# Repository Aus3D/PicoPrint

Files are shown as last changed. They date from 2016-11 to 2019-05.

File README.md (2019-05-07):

# PicoPrint

PicoPrint is a 32-bit 3D printer control board, designed to be fast, quiet, and compact.

PicoPrint is still in active development, and some specifications are not yet finalised. Once the design has been finalised, this page will be updated with detailed information.

## Image
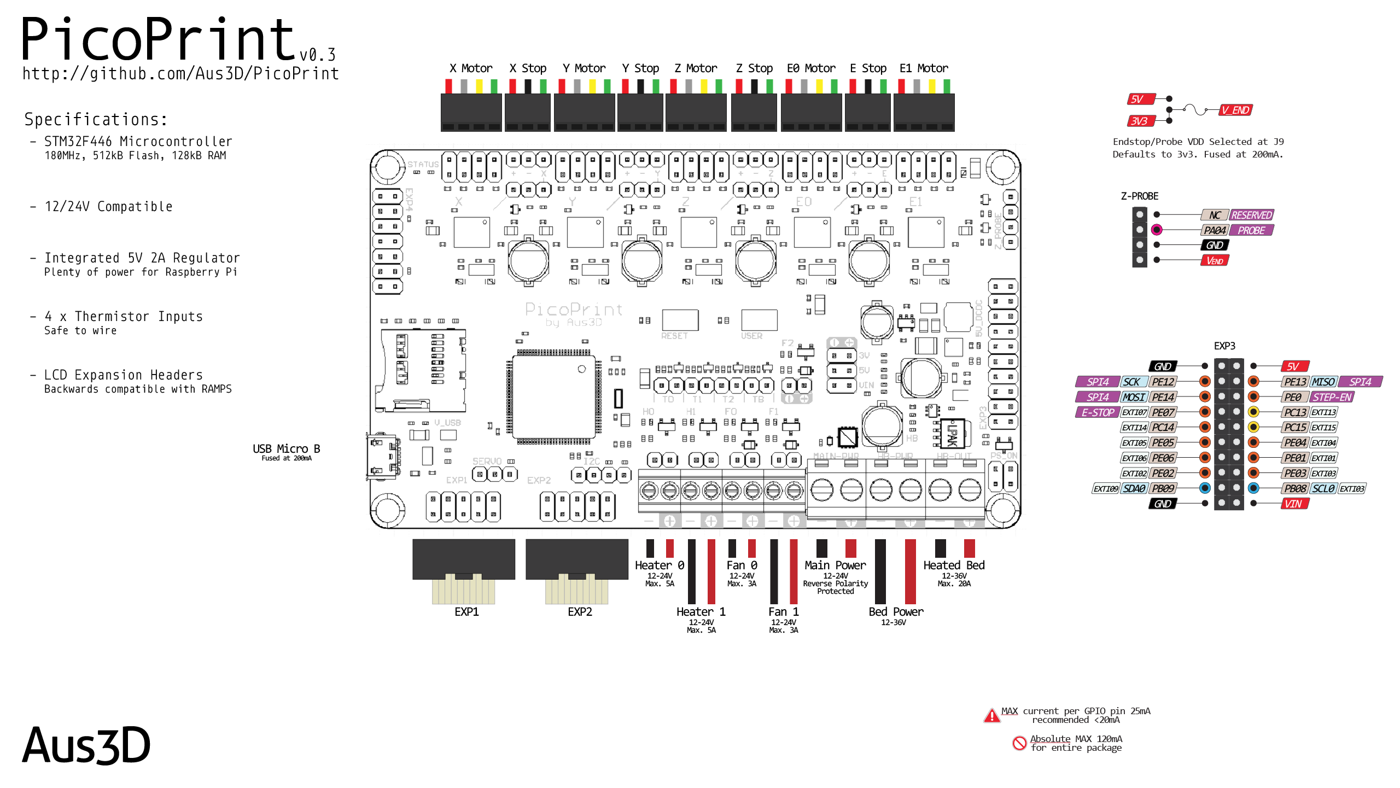
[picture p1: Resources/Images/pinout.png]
PicoPrint Pinout


## Specifications
* 32-bit STM32F446VET6 Microcontroller
  * 180MHz core clock speed
  * 512kB Flash Memory
  * 128kB SRAM
  * Floating Point Unit
* 5 x TMC2130 Stepper Drivers
  * STEP/DIR for motion + SPI bus for configuration
  * StealthChop for quiet printing
  * StallGuard signal wired to endstop inputs for sensorless homing (enabled by jumper)
* 1 x 20A MOSFET for Heated Bed
  * Low RDSon MOSFET for minimum heat dissipation
  * MOSFET driver IC for improved PWM performance
* 2 x 5A MOSFETs for Heater Cartridges
  * Accessible via screw terminal or pin header for pluggable cables
* 3 x 3A MOSFETs for Fans and Lighting
  * Suppresion diodes for flyback protection
  * Accessible via screw terminal (F0 & F1) or pin header (F0, F1 & F2)
* 12-24V Compatibility
  * Maximum 30V on main power rail
  * Maximum 40V on bed power rail
* Internal 5V 2A High-Efficiency Buck Regulator
  * Synchronous regulator for maximum efficiency
  * Up to 2A current draw
    * 200mA required for PicoPrint, 1.8A remaining for peripherals
    * Sufficient for most external LCDs, RC servo motors, or single-board computers (Raspberry Pi and similar)
* 4 x Thermistor Inputs
  * 2 HotEnds, 1 Bed + 1 Chamber/Spare
* 4 x Endstop Inputs
  * Jumper allows selection of either external endstop or TMC2130 StallGuard for sensorless homing for each endstop
* 1 x Z-Probe Connector
  * Includes 1 Interrupt-capable pin and one ADC-capable pin
* Rugged Design for Maximum Reliability
  * Power Rail Protection
    * Main power input is protected against reverse-polarity by P-Ch MOSFET
      * No fuse to replace if wiring is reversed
      * Red LED indicates reversed power polarity
    * 5V from USB is fused (200mA self-resetting PTC) to protect host device
    * 5V Buck Regulator implements overcurrent, overtemperature, and short-circuit protection
    * 3.3V Linear Regulator implements overcurrent and overtemperature protection
    * Main power input can be monitored by ADC channel to measure input voltage (firmware dependent)
  * Microcontroller Pin Protection
    * Dedicated ESD-protection IC on USB interface
    * Thermistors + Endstops + Z-Probe protected against accidental connection to ±30V by diode clipping circuit
      * Endstops are safe to use with 5/12/24V signals if desired

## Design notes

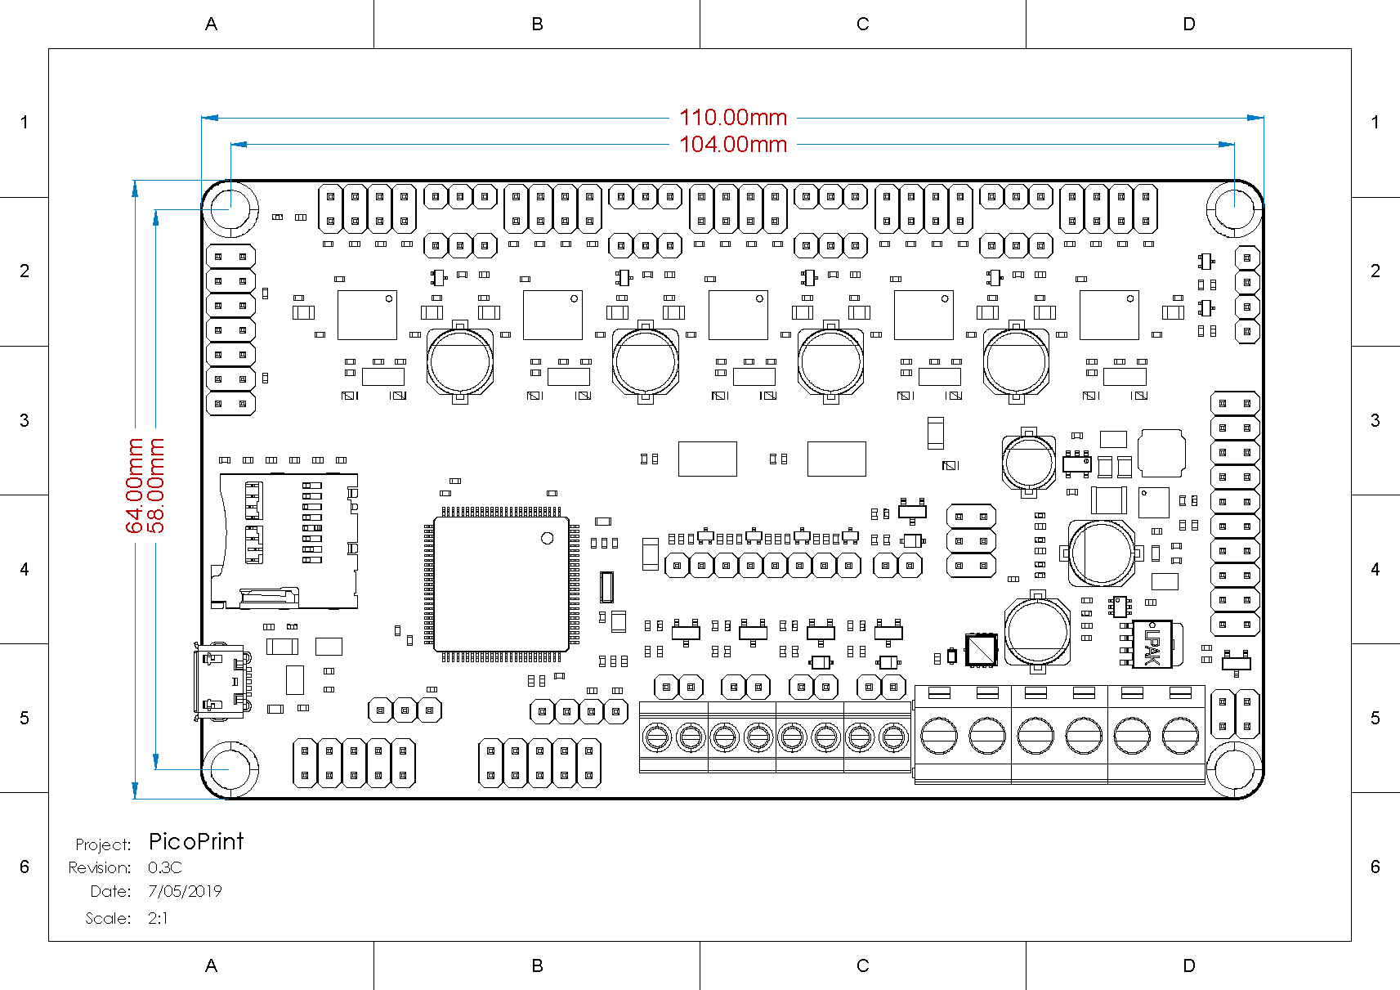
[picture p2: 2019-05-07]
Resources/Images/dimensions.png

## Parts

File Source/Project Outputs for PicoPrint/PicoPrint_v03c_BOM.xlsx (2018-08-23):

Designator | Description | Comment | Value | Quantity | Note | Manufacturer 1 | Manufacturer Part Number 1 | Supplier 1 | Supplier Part Number 1
C1, C8, C13, C14, C18, C25, C27, C48, C52, C56, C88, C92, C122, C123 | Capacitor (SMD Ceramic) | CapC-0402-4.7uF-10V | 4.7uF | 14 | Approved sub OK | Samsung (https://octopart-clicks.com/click/altium?sku=1276-1482-1-ND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) | CL05A475MP5NRNC (https://octopart-clicks.com/click/altium?sku=1276-1482-1-ND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) | Digi-Key | 1276-1482-1-ND (https://octopart-clicks.com/click/altium?sku=1276-1482-1-ND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)
C2, C3, C4, C5, C6, C7, C9, C11, C12, C19, C20, C21, C22, C23, C24, C45, C49, C53, C63, C64, C65, C72, C73, C74, C85, C89, C101, C102, C107, C108, C115, C124 | Capacitor (SMD Ceramic) | CapC-0402-100nF | 100nF | 32 | Approved sub OK | Yageo (https://octopart-clicks.com/click/altium?sku=311-1336-1-ND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) | CC0402KRX5R6BB104 (https://octopart-clicks.com/click/altium?sku=311-1336-1-ND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) | Digi-Key | 311-1336-1-ND (https://octopart-clicks.com/click/altium?sku=311-1336-1-ND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)
C10, C15, C16, C26 | Capacitor (SMD Ceramic) | CapC-0402-1uF-10V | 1uF | 4 | Approved sub OK | Samsung (https://octopart-clicks.com/click/altium?sku=1276-1448-1-ND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) | CL05A105MP5NNNC (https://octopart-clicks.com/click/altium?sku=1276-1448-1-ND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) | Digi-Key | 1276-1448-1-ND (https://octopart-clicks.com/click/altium?sku=1276-1448-1-ND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)
C17 | Capacitor (SMD Ceramic) | CapC-0805-10uF 6.3V | 10uF | 1 | Approved sub OK | Samsung (https://octopart-clicks.com/click/altium?sku=1276-6457-1-ND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) | CL21A106KQFNNNG (https://octopart-clicks.com/click/altium?sku=1276-6457-1-ND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) | Digi-Key | 1276-6457-1-ND (https://octopart-clicks.com/click/altium?sku=1276-6457-1-ND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)
C29, C31, C33, C75, C77 | Capacitor (SMD Ceramic) | CapC-0402-22nF-50V | 22nF | 5 | Approved sub OK | Murata (https://octopart-clicks.com/click/altium?sku=490-3884-1-ND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) | GRM155R71H223KA12D (https://octopart-clicks.com/click/altium?sku=490-3884-1-ND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) | Digi-Key | 490-3884-1-ND (https://octopart-clicks.com/click/altium?sku=490-3884-1-ND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)
C30, C32, C34, C35, C36, C39, C40, C42, C43, C76, C78, C79, C80, C82, C83, C113, C117 | Capacitor (SMD Ceramic) | CapC-0402-100nF-50V | 100nF | 17 | Approved sub OK | Murata (https://octopart-clicks.com/click/altium?sku=490-10700-1-ND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) | GRM155R71H104KE14D (https://octopart-clicks.com/click/altium?sku=490-10700-1-ND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) | Digi-Key | 490-10700-1-ND (https://octopart-clicks.com/click/altium?sku=490-10700-1-ND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)
C37, C38, C41, C44, C81, C84, C110, C114, C125, C126, C127 | Capacitor (SMD Ceramic) | CapC-0603-1uF 50V | 1uF | 11 | Approved sub OK | Samsung (https://octopart-clicks.com/click/altium?sku=1276-1860-1-ND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) | CL10A105KB8NNNC (https://octopart-clicks.com/click/altium?sku=1276-1860-1-ND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) | Digi-Key | 1276-1860-1-ND (https://octopart-clicks.com/click/altium?sku=1276-1860-1-ND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)
C46, C50, C54, C86, C90 | Capacitor (SMD Ceramic) | CapC-0402-470nF | 470nF | 5 | Approved sub OK | Samsung (https://octopart-clicks.com/click/altium?sku=1276-1173-1-ND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) | CL05A474KP5NNNC (https://octopart-clicks.com/click/altium?sku=1276-1173-1-ND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) | Digi-Key | 1276-1173-1-ND (https://octopart-clicks.com/click/altium?sku=1276-1173-1-ND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)
C57, C58, C59, C60, C61, C62, C66, C67, C68, C69, C70, C71, C97, C98, C99, C100, C103, C104, C105, C106 | Capacitor (SMD Ceramic) | CapC-0402-470pF-100V | 470pF | 20 | Approved sub OK | Murata (https://octopart-clicks.com/click/altium?sku=490-6369-1-ND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) | GRM155R72A471KA01D (https://octopart-clicks.com/click/altium?sku=490-6369-1-ND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) | Digi-Key | 490-6369-1-ND (https://octopart-clicks.com/click/altium?sku=490-6369-1-ND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)
C93, C94, C95, C96, C112, C118 | Capacitor (SMD Polarised Electrolytic) | CapE-6.3-100uF-35V | 100uF 35V | 6 | Approved sub OK | Panasonic (https://octopart-clicks.com/click/altium?sku=PCE5016CT-ND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) | EEE-FT1V101AP (https://octopart-clicks.com/click/altium?sku=PCE5016CT-ND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) | Digi-Key | PCE5016CT-ND (https://octopart-clicks.com/click/altium?sku=PCE5016CT-ND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)
C116 | Capacitor (SMD Polarised Electrolytic) | CapE-5.0-100uF-6.3V | 100uF 6.3V | 1 | Approved sub OK | United Chemi-Con (https://octopart-clicks.com/click/altium?manufacturer=United%20Chemi-Con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) | EMVA6R3ADA101ME55G (https://octopart-clicks.com/click/altium?manufacturer=United%20Chemi-Con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) | Digi-Key | 565-2057-1-ND (https://octopart-clicks.com/click/altium?manufacturer=United%20Chemi-Con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)
C119 | Capacitor (SMD Ceramic) | CapC-1210-4.7uF-50V | 4.7uF | 1 | Approved sub OK | Murata (https://octopart-clicks.com/click/altium?sku=490-1864-1-ND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) | GRM32ER71H475KA88L (https://octopart-clicks.com/click/altium?sku=490-1864-1-ND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) | Digi-Key | 490-1864-1-ND (https://octopart-clicks.com/click/altium?sku=490-1864-1-ND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)
C120, C121 | Capacitor (SMD Ceramic) | CapC-0805-22uF 6.3V | 22uF | 2 | Approved sub OK | Samsung (https://octopart-clicks.com/click/altium?sku=1276-6460-1-ND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) | CL21A226MQQNNNG (https://octopart-clicks.com/click/altium?sku=1276-6460-1-ND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) | Digi-Key | 1276-6460-1-ND (https://octopart-clicks.com/click/altium?sku=1276-6460-1-ND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)
D1, D2, D3, D4, D5, D6, D7, D8, D9, D10 | Diode (SMD) | Dual Schottky 100mA 30V SOT523 |  | 10 | Approved sub OK | MCC (https://octopart-clicks.com/click/altium?sku=BAT54ST-TPCT-ND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) | BAT54ST-TP (https://octopart-clicks.com/click/altium?sku=BAT54ST-TPCT-ND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) | Digi-Key | BAT54ST-TPCT-ND (https://octopart-clicks.com/click/altium?sku=BAT54ST-TPCT-ND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)
D11, D12, D13 | Diode (SMD) | General 500mW 75V SOD323 | Vf=1V @ 50mA | 3 | Approved sub OK | MCC (https://octopart-clicks.com/click/altium?sku=1N4148WXTPMSCT-ND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) | 1N4148WX-TP (https://octopart-clicks.com/click/altium?sku=1N4148WXTPMSCT-ND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) | Digi-Key | 1N4148WXTPMSCT-ND (https://octopart-clicks.com/click/altium?sku=1N4148WXTPMSCT-ND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)
D14, D15, D16 | Diode (SMD) | Schottky 2A 40V SOD-123F |  | 3 | Approved sub OK | ON Semiconductor / Fairchild (https://octopart-clicks.com/click/altium?manufacturer=ON%20Semiconductor%20%2F%20Fairchild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) | SS24FL (https://octopart-clicks.com/click/altium?manufacturer=ON%20Semiconductor%20%2F%20Fairchild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) | Digi-Key | SS24FLCT-ND (https://octopart-clicks.com/click/altium?manufacturer=ON%20Semiconductor%20%2F%20Fairchild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)
D17 | Diode (SMD) | Zener 10V 150mW SOD523 |  | 1 | Approved sub OK | Panasonic SSG (https://octopart-clicks.com/click/altium?sku=DZ2S100M0LCT-ND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) | DZ2S100M0L (https://octopart-clicks.com/click/altium?sku=DZ2S100M0LCT-ND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) | Digi-Key | DZ2S100M0LCT-ND (https://octopart-clicks.com/click/altium?sku=DZ2S100M0LCT-ND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)
F1, F3 | Fuse - 30V 400mA Trip PTC SMD 1206 | PTC Resettable Fuse | 200mA | 2 | Approved sub OK | Bel (https://octopart-clicks.com/click/altium?sku=507-1797-1-ND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) | 0ZCJ0020FF2E (https://octopart-clicks.com/click/altium?sku=507-1797-1-ND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) | Digi-Key | 507-1797-1-ND (https://octopart-clicks.com/click/altium?sku=507-1797-1-ND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)
FB1, FB3, FB4 | Ferrite bead 120 Ohm at 100 MHz 2A 0603 SMD | 120R @ 100 MHz | 120R @ 100 MHz | 3 | Approved sub OK, [NoParam] | Murata (https://octopart-clicks.com/click/altium?sku=490-1037-1-ND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) | BLM18PG-121SN1D (https://octopart-clicks.com/click/altium?sku=490-1037-1-ND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) | Digi-Key | 490-1037-1-ND (https://octopart-clicks.com/click/altium?sku=490-1037-1-ND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)
FB2 | Ferrite bead 50 Ohm at 100 MHz 6A 1206 SMD | 50R @ 100 MHz | 50R @ 100 MHz | 1 | Approved sub OK | Laird (https://octopart-clicks.com/click/altium?sku=240-2412-1-ND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) | HI1206T500R-10 (https://octopart-clicks.com/click/altium?sku=240-2412-1-ND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) | Digi-Key | 240-2412-1-ND (https://octopart-clicks.com/click/altium?sku=240-2412-1-ND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)
J1 |  | Micro-USB B Socket |  | 1 | Approved sub OK | Molex (https://octopart-clicks.com/click/altium?sku=WM1399CT-ND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) | 105017-0001 (https://octopart-clicks.com/click/altium?sku=WM1399CT-ND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) | Digi-Key | WM1399CT-ND (https://octopart-clicks.com/click/altium?sku=WM1399CT-ND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)
L2 | 4.7µH Shielded Wirewound Inductor 2.6A 35 mOhm Nonstandard | Inductor SMD 4.7uH 2.6A | 4.7uH | 1 | Approved sub OK | Taiyo Yuden (https://octopart-clicks.com/click/altium?sku=587-3461-1-ND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) | NRS5030T4R7MMGJ (https://octopart-clicks.com/click/altium?sku=587-3461-1-ND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) | Digi-Key | 587-3461-1-ND (https://octopart-clicks.com/click/altium?sku=587-3461-1-ND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)
LD1 | LED (SMD) | LED-0402 | Red | 1 | Approved sub OK | Wurth Electronics (https://octopart-clicks.com/click/altium?sku=732-11991-1-ND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) | 150040RS73240 (https://octopart-clicks.com/click/altium?sku=732-11991-1-ND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) | Digi-Key | 732-11991-1-ND (https://octopart-clicks.com/click/altium?sku=732-11991-1-ND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)
LD2, LD3, LD4, LD5, LD6, LD8, LD9, LD10, LD11, LD12, LD13 | LED (SMD) | LED-0402 | Green | 11 | Approved sub OK | Wurth Electronics (https://octopart-clicks.com/click/altium?sku=732-11992-1-ND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) | 150040VS73240 (https://octopart-clicks.com/click/altium?sku=732-11992-1-ND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) | Digi-Key | 732-11992-1-ND (https://octopart-clicks.com/click/altium?sku=732-11992-1-ND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)
LD7 | LED (SMD) | LED-0402 | Yellow | 1 | Approved sub OK | Wurth Electronics (https://octopart-clicks.com/click/altium?sku=732-11993-1-ND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) | 150040YS73240 (https://octopart-clicks.com/click/altium?sku=732-11993-1-ND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) | Digi-Key | 732-11993-1-ND (https://octopart-clicks.com/click/altium?sku=732-11993-1-ND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)
P1, P4, P11 | Screw Terminal 5mm 2-Way | Main PWR Screw Term, Bed PWR Screw Term, HB Screw Term |  | 3 |  | Phoenix Contact (https://octopart-clicks.com/click/altium?sku=277-6405-ND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) | 1935776 (https://octopart-clicks.com/click/altium?sku=277-6405-ND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) | Digi-Key | 277-6405-ND (https://octopart-clicks.com/click/altium?sku=277-6405-ND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)
P2, P3, P6, P9, P29, P37, P38, P39, P40 | Header, 3-Pin | X-STOP, E-STOP, Y_STOP, Z-STOP, SERVO, X_STOP_SEL, Y_STOP_SEL, Z_STOP_SEL, E_STOP_SEL |  | 9 | Approved sub OK | Generic Header
P5, P10 | Header, 5-Pin, Dual row | EXP1, EXP2 |  | 2 | Approved sub OK | Generic Header
P7, P28 | Header, 3-Pin, Dual row | PWR_AUX, Header 2X2 |  | 2 | Approved sub OK | Generic Header
P8, P30 | Header, 4-Pin | PROBE, I2C |  | 2 | Approved sub OK | Generic Header
P12, P16, P19, P24, P32 | Header, 2-Pin | H0 Header, H1 Header, F0 Header, F1 Header, F2 Header |  | 5 | Approved sub OK | Generic Header
P13 | Header, 10-Pin, Dual row | EXP3 |  | 1 | Approved sub OK | Generic Header
P14 | Header, 8-Pin | Thermistors |  | 1 | Approved sub OK | Generic Header
P15, P17, P22, P26 | Screw Terminal 3.5mm 2-Way | H0 Screw Term, H1 Screw Term, F0 Screw Term, F1 Screw Term |  | 4 |  | Phoenix Contact (https://octopart-clicks.com/click/altium?sku=277-1721-ND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) | 1984617 (https://octopart-clicks.com/click/altium?sku=277-1721-ND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) | Digi-Key | 277-1721-ND (https://octopart-clicks.com/click/altium?sku=277-1721-ND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)
P18 | Header, 7-Pin, Dual row | EXP4 |  | 1 | Approved sub OK | Generic Header
P20, P23, P27, P33, P35 | Header, 4-Pin, Dual row | X-MOTOR, Y-MOTOR, Z-MOTOR, E0-MOTOR, E1-MOTOR |  | 5 | Approved sub OK | Generic Header
Q1, Q2, Q3, Q4, Q8, Q9 | N-CH MOSFET 30V 5.7A SOT23 | AO3400A |  | 6 |  | Alpha & Omega Semiconductor (https://octopart-clicks.com/click/altium?manufacturer=Alpha%20%26%20Omega%20Semiconductor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) | AO3400A (https://octopart-clicks.com/click/altium?manufacturer=Alpha%20%26%20Omega%20Semiconductor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) | Digi-Key | 785-1000-1-ND (https://octopart-clicks.com/click/altium?manufacturer=Alpha%20%26%20Omega%20Semiconductor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)
Q5 | N-CH MOSFET 40V 100A LFPAK | BUK9Y4R4-40E |  | 1 |  | NXP Semiconductors (https://octopart-clicks.com/click/altium?manufacturer=NXP%20Semiconductors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) | BUK9Y4R4-40E,115 (https://octopart-clicks.com/click/altium?manufacturer=NXP%20Semiconductors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) | Digi-Key | 1727-1502-1-ND (https://octopart-clicks.com/click/altium?manufacturer=NXP%20Semiconductors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)
Q7 | MOSFET SMD P-CH 30V 60A PowerPAK1212 | SI7111EDN-T1-GE3 |  | 1 |  | Vishay (https://octopart-clicks.com/click/altium?sku=SI7111EDN-T1-GE3CT-ND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) | SI7111EDN-T1-GE3 (https://octopart-clicks.com/click/altium?sku=SI7111EDN-T1-GE3CT-ND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) | Digi-Key | SI7111EDN-T1-GE3CT-ND (https://octopart-clicks.com/click/altium?sku=SI7111EDN-T1-GE3CT-ND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)
R1, R2, R8, R13, R15, R20, R22, R25, R28, R32, R34 | Resistor | Res-0402-4K7 | 4K7 | 11 | Approved sub OK | Yageo (https://octopart-clicks.com/click/altium?sku=311-4.7KJRCT-ND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) | RC0402JR-074K7L (https://octopart-clicks.com/click/altium?sku=311-4.7KJRCT-ND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) | Digi-Key | 311-4.7KJRCT-ND (https://octopart-clicks.com/click/altium?sku=311-4.7KJRCT-ND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)
R3, R4, R5, R19, R37, R38, R43, R44, R48, R51, R53, R68 | Resistor | Res-0402-1K | 1K | 12 | Approved sub OK | Yageo (https://octopart-clicks.com/click/altium?sku=311-1.0KJRCT-ND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) | RC0402JR-071KL (https://octopart-clicks.com/click/altium?sku=311-1.0KJRCT-ND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) | Digi-Key | 311-1.0KJRCT-ND (https://octopart-clicks.com/click/altium?sku=311-1.0KJRCT-ND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)
R6, R7, R14 | Resistor | Res-0402-470R | 470R | 3 | Approved sub OK | Yageo (https://octopart-clicks.com/click/altium?sku=311-470JRCT-ND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) | RC0402JR-07470RL (https://octopart-clicks.com/click/altium?sku=311-470JRCT-ND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) | Digi-Key | 311-470JRCT-ND (https://octopart-clicks.com/click/altium?sku=311-470JRCT-ND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)
R9, R10 | Resistor | Res-0402-2K2 | 2K2 | 2 | Approved sub OK | Yageo (https://octopart-clicks.com/click/altium?sku=311-2.2KJRCT-ND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) | RC0402JR-072K2L (https://octopart-clicks.com/click/altium?sku=311-2.2KJRCT-ND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) | Digi-Key | 311-2.2KJRCT-ND (https://octopart-clicks.com/click/altium?sku=311-2.2KJRCT-ND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)
R11, R12 | Resistor | Res-0402-100R | 100R | 2 | Approved sub OK | Yageo (https://octopart-clicks.com/click/altium?sku=311-100JRCT-ND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) | RC0402JR-07100RL (https://octopart-clicks.com/click/altium?sku=311-100JRCT-ND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) | Digi-Key | 311-100JRCT-ND (https://octopart-clicks.com/click/altium?sku=311-100JRCT-ND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)
R16, R17, R70 | Resistor | Res-0402-47K | 47K | 3 | Approved sub OK | Yageo (https://octopart-clicks.com/click/altium?sku=311-47KJRCT-ND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) | RC0402JR-0747KL (https://octopart-clicks.com/click/altium?sku=311-47KJRCT-ND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) | Digi-Key | 311-47KJRCT-ND (https://octopart-clicks.com/click/altium?sku=311-47KJRCT-ND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)
R18, R21, R23, R26, R65, R69 | Resistor | Res-0402-10K | 10K | 6 | Approved sub OK | Yageo (https://octopart-clicks.com/click/altium?sku=311-10KJRCT-ND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) | RC0402JR-0710KL (https://octopart-clicks.com/click/altium?sku=311-10KJRCT-ND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) | Digi-Key | 311-10KJRCT-ND (https://octopart-clicks.com/click/altium?sku=311-10KJRCT-ND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)
R24, R27, R31, R33 | Resistor | Res-0402-4K7 | 4K7 1% | 4 | Approved sub OK | Yageo (https://octopart-clicks.com/click/altium?sku=311-4.7KJRCT-ND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) | RC0402JR-074K7L (https://octopart-clicks.com/click/altium?sku=311-4.7KJRCT-ND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) | Digi-Key | 311-4.7KJRCT-ND (https://octopart-clicks.com/click/altium?sku=311-4.7KJRCT-ND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)
R29, R30 | Resistor | Res-0402-22R | 22R | 2 | Approved sub OK | Yageo (https://octopart-clicks.com/click/altium?sku=311-22JRCT-ND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) | RC0402JR-0722RL (https://octopart-clicks.com/click/altium?sku=311-22JRCT-ND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) | Digi-Key | 311-22JRCT-ND (https://octopart-clicks.com/click/altium?sku=311-22JRCT-ND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)
R35, R36, R41, R42, R47, R50 | Resistor | Res-0402-10R | 10R | 6 | Approved sub OK | Yageo (https://octopart-clicks.com/click/altium?sku=311-10JRCT-ND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) | RC0402JR-0710RL (https://octopart-clicks.com/click/altium?sku=311-10JRCT-ND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) | Digi-Key | 311-10JRCT-ND (https://octopart-clicks.com/click/altium?sku=311-10JRCT-ND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)
R39, R40, R45, R46, R49, R52, R54, R67 | Resistor | Res-0402-100K | 100K | 8 | Approved sub OK | Yageo (https://octopart-clicks.com/click/altium?sku=311-100KJRCT-ND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) | RC0402JR-07100KL (https://octopart-clicks.com/click/altium?sku=311-100KJRCT-ND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) | Digi-Key | 311-100KJRCT-ND (https://octopart-clicks.com/click/altium?sku=311-100KJRCT-ND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)
R55, R56, R57, R58, R59, R60, R61, R62, R63, R64 | Resistor | Res-0805-0R11-0.333W | 0R11 1% | 10 | Approved sub OK | Susumu (https://octopart-clicks.com/click/altium?sku=RL12S.11FCT-ND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) | RL1220S-R11-F (https://octopart-clicks.com/click/altium?sku=RL12S.11FCT-ND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) | Digi-Key | RL12S.11FCT-ND (https://octopart-clicks.com/click/altium?sku=RL12S.11FCT-ND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)
R66 | Resistor | Res-0402-49.9K | 49.9K | 1 | Approved sub OK | Yageo (https://octopart-clicks.com/click/altium?sku=311-2296-1-ND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) | RT0402DRE0749K9L (https://octopart-clicks.com/click/altium?sku=311-2296-1-ND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) | Digi-Key | 311-2296-1-ND (https://octopart-clicks.com/click/altium?sku=311-2296-1-ND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)
S1, S2 | SMD Button | User, Reset |  | 2 | Approved sub OK | APEM (https://octopart-clicks.com/click/altium?sku=679-2396-1-ND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) | MJTP1106SATR (https://octopart-clicks.com/click/altium?sku=679-2396-1-ND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) | Digi-Key | 679-2396-1-ND (https://octopart-clicks.com/click/altium?sku=679-2396-1-ND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)
U1 | ARM Cortex-M4 32-bit MCU+FPU, 210 DMIPS, 512 kB Flash, 128 kB Internal RAM, 81 I/Os, 100-pin LQFP, -40 to 105 degC, Tray | STM32F446VET6 |  | 1 |  | STMicroelectronics (https://octopart-clicks.com/click/altium?sku=497-15375-ND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) | STM32F446VET6 (https://octopart-clicks.com/click/altium?sku=497-15375-ND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) | Digi-Key | 497-15375-ND (https://octopart-clicks.com/click/altium?sku=497-15375-ND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)
U2 | MicroSD Card Socket | MICROSD |  | 1 | Approved sub OK | Amphenol (https://octopart-clicks.com/click/altium?sku=101-00660-68-6-1-ND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) | 10100660686 (https://octopart-clicks.com/click/altium?sku=101-00660-68-6-1-ND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) | Digi-Key | 101-00660-68-6-1-ND (https://octopart-clicks.com/click/altium?sku=101-00660-68-6-1-ND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)
U3 | ESD Protection IC | USBLC6 USB ESD Protection |  | 1 |  | STMicroelectronics (https://octopart-clicks.com/click/altium?sku=497-5235-1-ND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) | USBLC6-2SC6 (https://octopart-clicks.com/click/altium?sku=497-5235-1-ND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) | Digi-Key | 497-5235-1-ND (https://octopart-clicks.com/click/altium?sku=497-5235-1-ND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)
U4 | MOSFET Gate Driver IC | Gate Driver |  | 1 |  | Diodes (https://octopart-clicks.com/click/altium?sku=ZXGD3009DYTADICT-ND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) | ZXGD3009DYTA (https://octopart-clicks.com/click/altium?sku=ZXGD3009DYTADICT-ND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) | Digi-Key | ZXGD3009DYTADICT-ND (https://octopart-clicks.com/click/altium?sku=ZXGD3009DYTADICT-ND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)
U5, U6, U7, U8, U9 | Stepper Driver IC | TMC2130-LA |  | 5 |  | Trinamic (https://octopart-clicks.com/click/altium?sku=1460-1130-1-ND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) | TMC2130-LA-T (https://octopart-clicks.com/click/altium?sku=1460-1130-1-ND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) | Digi-Key | 1460-1130-1-ND (https://octopart-clicks.com/click/altium?sku=1460-1130-1-ND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)
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

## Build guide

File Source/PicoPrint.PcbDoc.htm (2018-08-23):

Reporting Options

# File in Previous Format

Date | : | 23/08/2018
Time | : | 1:22:07 PM
Filename | : | G:\Git\R32-Micro\Source\PicoPrint.PcbDoc

Version | Warning

This file was generated by an earlier version of the software

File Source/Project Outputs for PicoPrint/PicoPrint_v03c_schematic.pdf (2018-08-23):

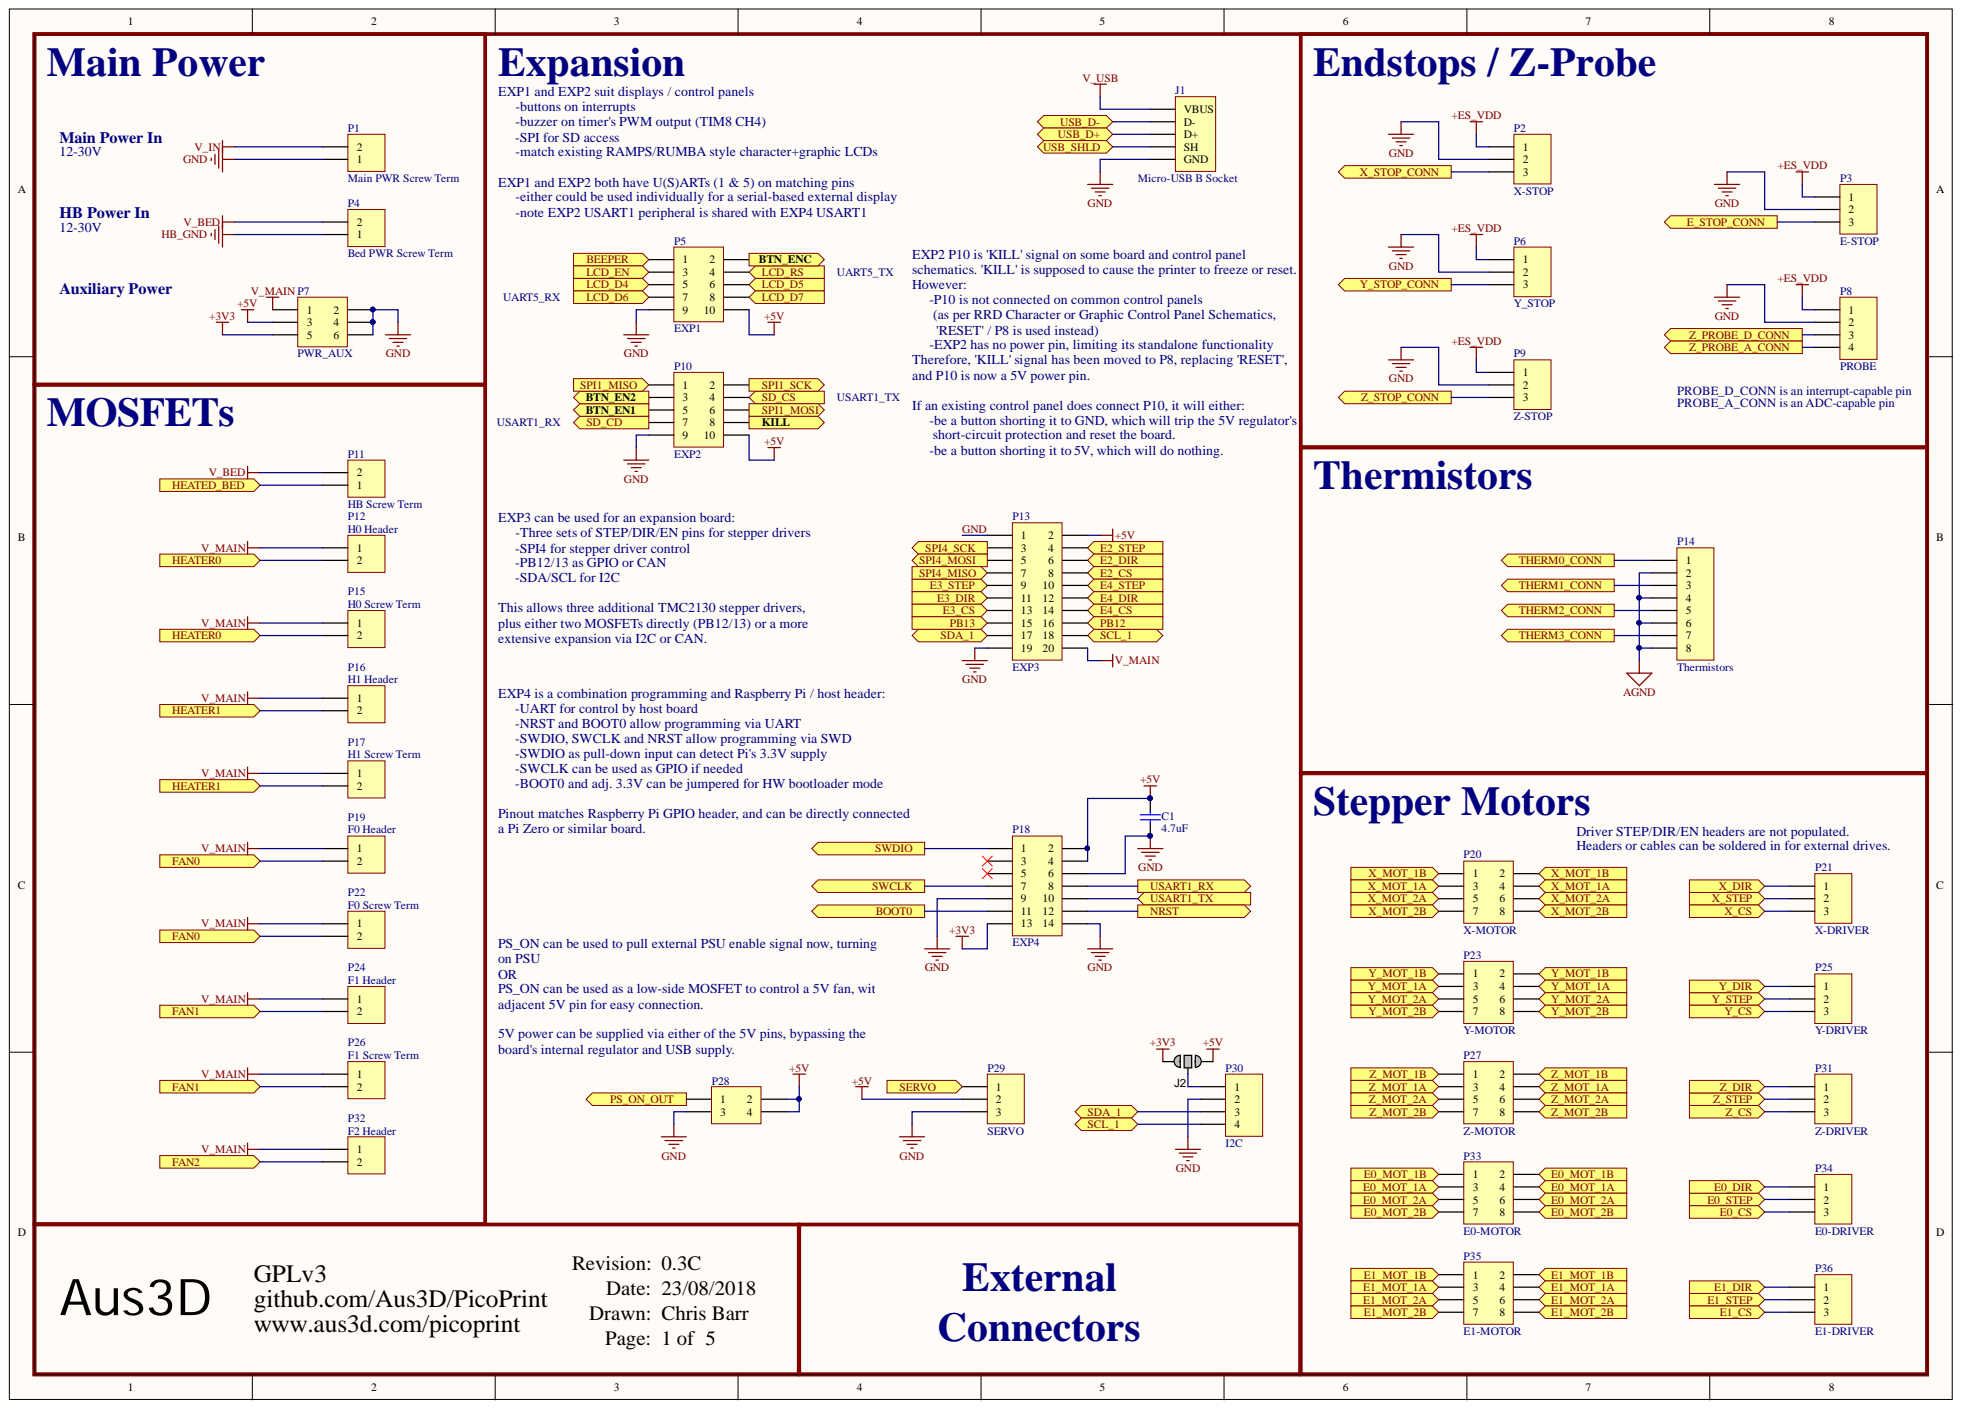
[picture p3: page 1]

EXP1 and EXP2 suit displays / control panels
-buttons on interrupts
-buzzer on timer's PWM output (TIM8 CH4)
-SPI for SD access
-match existing RAMPS/RUMBA style character+graphic LCDs

EXP1 and EXP2 both have U(S)ARTs (1 & 5) on matching pins
-either could be used individually for a serial-based external display
-note EXP2 USART1 peripheral is shared with EXP4 USART1

EXP2 P10 is 'KILL' signal on some board and control panel
schematics. 'KILL' is supposed to cause the printer to freeze or reset.
However:
-P10 is not connected on common control panels
(as per RRD Character or Graphic Control Panel Schematics,
'RESET' / P8 is used instead)
-EXP2 has no power pin, limiting its standalone functionality
Therefore, 'KILL' signal has been moved to P8, replacing 'RESET',
and P10 is now a 5V power pin.

PROBE_D_CONN is an interrupt-capable pin
PROBE_A_CONN is an ADC-capable pin

If an existing control panel does connect P10, it will either:
-be a button shorting it to GND, which will trip the 5V regulator's
short-circuit protection and reset the board.
-be a button shorting it to 5V, which will do nothing.

EXP3 can be used for an expansion board:
-Three sets of STEP/DIR/EN pins for stepper drivers
-SPI4 for stepper driver control
-PB12/13 as GPIO or CAN
-SDA/SCL for I2C

This allows three additional TMC2130 stepper drivers,
plus either two MOSFETs directly (PB12/13) or a more
extensive expansion via I2C or CAN.

EXP4 is a combination programming and Raspberry Pi / host header:
-UART for control by host board
-NRST and BOOT0 allow programming via UART
-SWDIO, SWCLK and NRST allow programming via SWD
-SWDIO as pull-down input can detect Pi's 3.3V supply
-SWCLK can be used as GPIO if needed
-BOOT0 and adj. 3.3V can be jumpered for HW bootloader mode

Pinout matches Raspberry Pi GPIO header, and can be directly connected t
a Pi Zero or similar board.

Driver STEP/DIR/EN headers are not populated.
Headers or cables can be soldered in for external drives.

PS_ON can be used to pull external PSU enable signal now, turning
on PSU
PS_ON can be used as a low-side MOSFET to control a 5V fan, wit
adjacent 5V pin for easy connection.

5V power can be supplied via either of the 5V pins, bypassing the
board's internal regulator and USB supply.

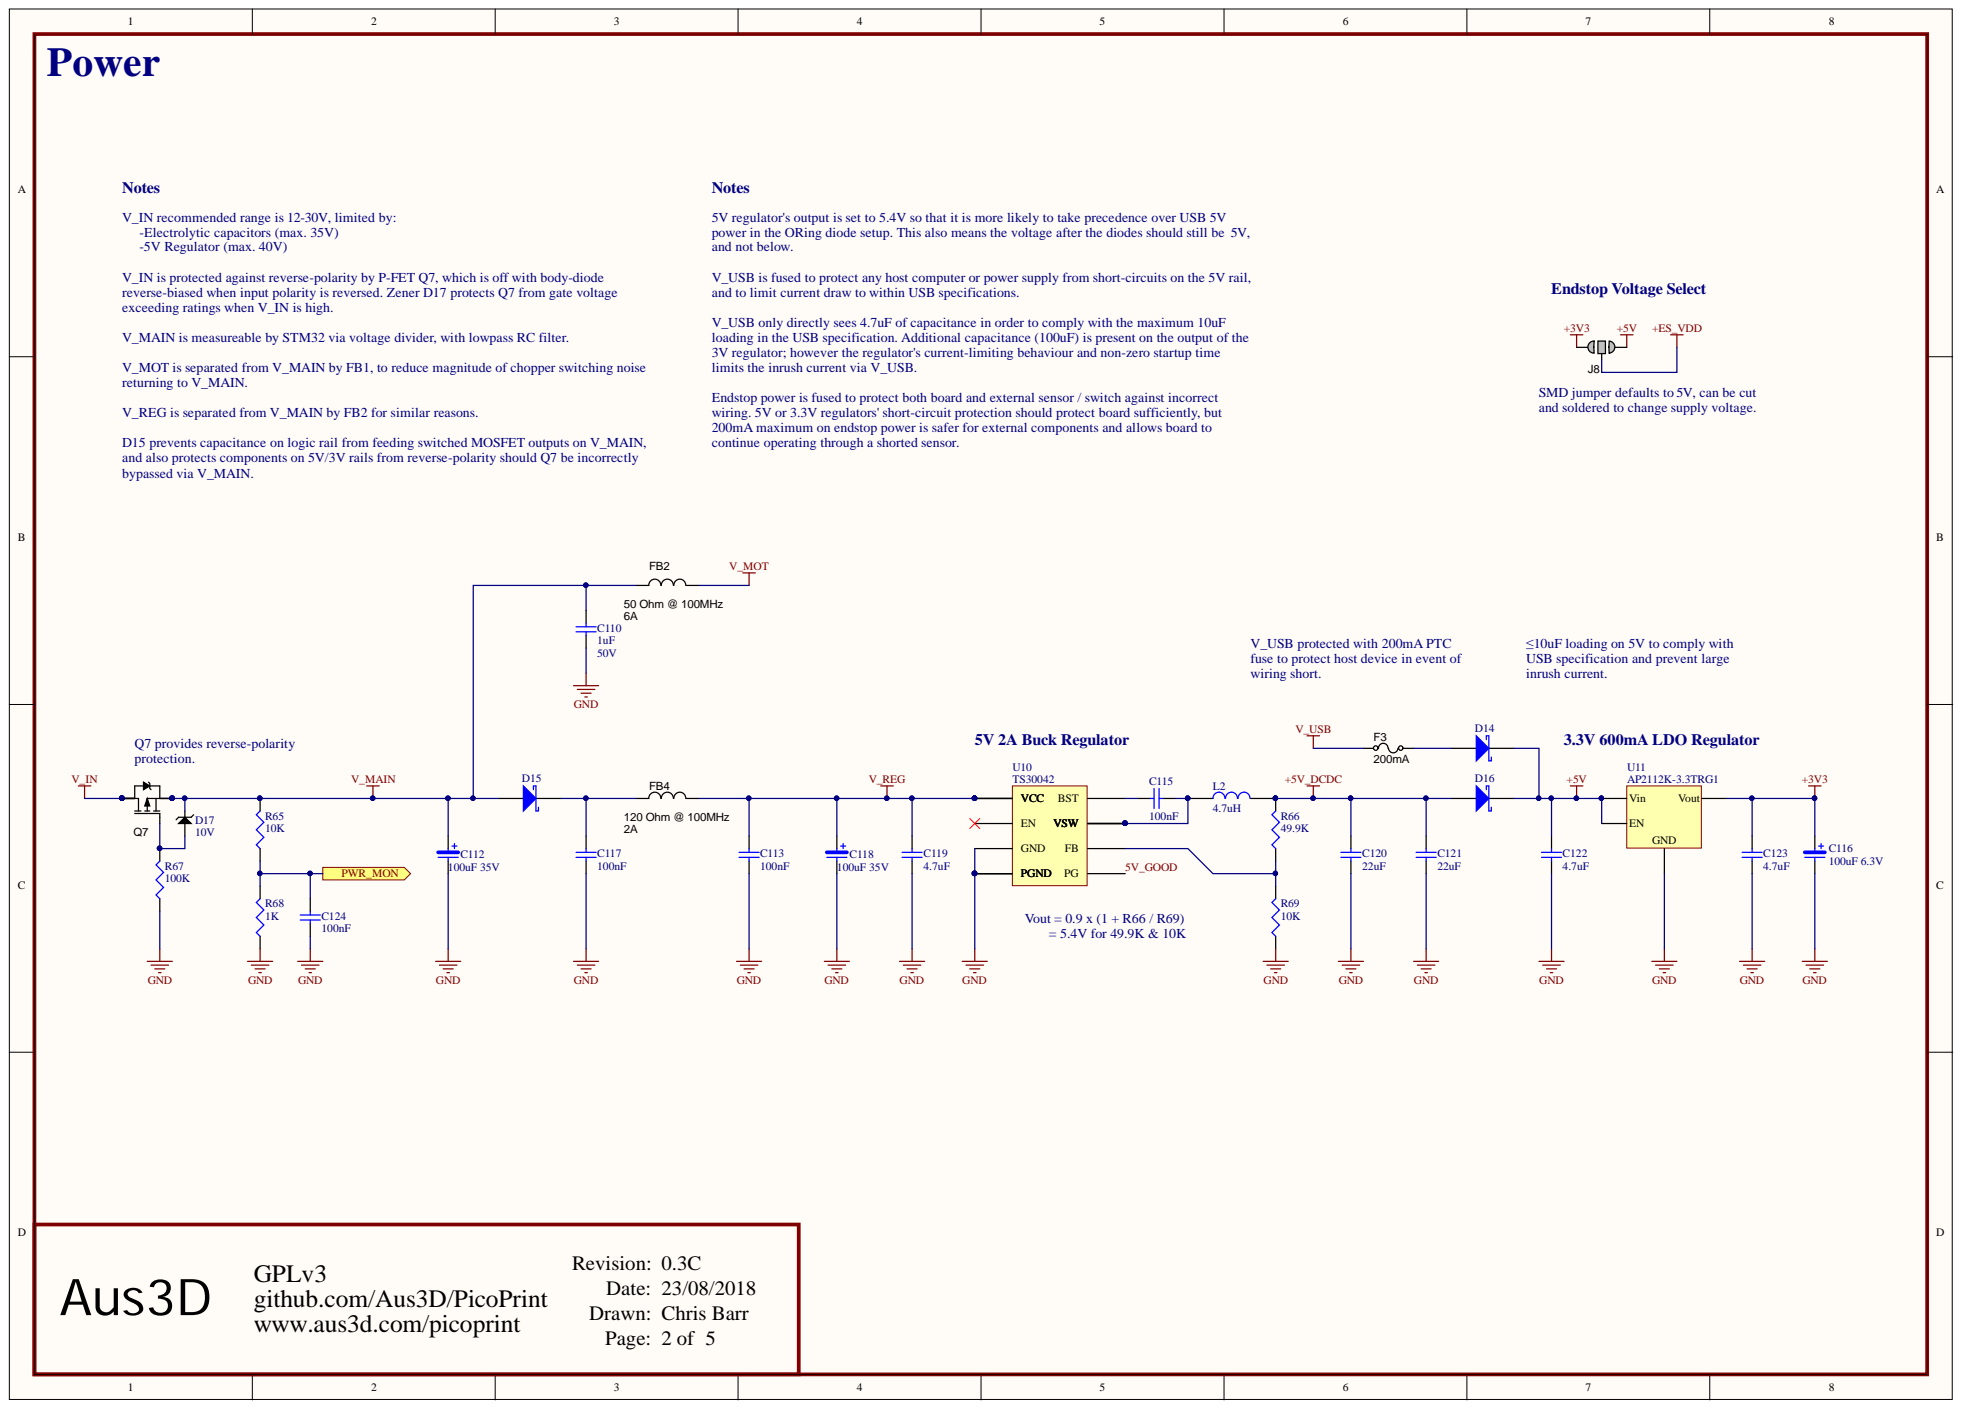
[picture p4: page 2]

V_IN recommended range is 12-30V, limited by:
-Electrolytic capacitors (max. 35V)
-5V Regulator (max. 40V)

5V regulator's output is set to 5.4V so that it is more likely to take precedence over USB 5V
power in the ORing diode setup. This also means the voltage after the diodes should still be 5V,
and not below.

V_IN is protected against reverse-polarity by P-FET Q7, which is off with body-diode
reverse-biased when input polarity is reversed. Zener D17 protects Q7 from gate voltage
exceeding ratings when V_IN is high.

V_USB is fused to protect any host computer or power supply from short-circuits on the 5V rail,
and to limit current draw to within USB specifications.

V_USB only directly sees 4.7uF of capacitance in order to comply with the maximum 10uF
loading in the USB specification. Additional capacitance (100uF) is present on the output of the
3V regulator; however the regulator's current-limiting behaviour and non-zero startup time
limits the inrush current via V_USB.

V_MAIN is measureable by STM32 via voltage divider, with lowpass RC filter.

V_MOT is separated from V_MAIN by FB1, to reduce magnitude of chopper switching noise
returning to V_MAIN.

Endstop power is fused to protect both board and external sensor / switch against incorrect
wiring. 5V or 3.3V regulators' short-circuit protection should protect board sufficiently, but
200mA maximum on endstop power is safer for external components and allows board to
continue operating through a shorted sensor.

SMD jumper defaults to 5V, can be cut
and soldered to change supply voltage.

V_REG is separated from V_MAIN by FB2 for similar reasons.

D15 prevents capacitance on logic rail from feeding switched MOSFET outputs on V_MAIN,
and also protects components on 5V/3V rails from reverse-polarity should Q7 be incorrectly
bypassed via V_MAIN.

V_USB protected with 200mA PTC
fuse to protect host device in event of
wiring short.

≤10uF loading on 5V to comply with
USB specification and prevent large
inrush current.

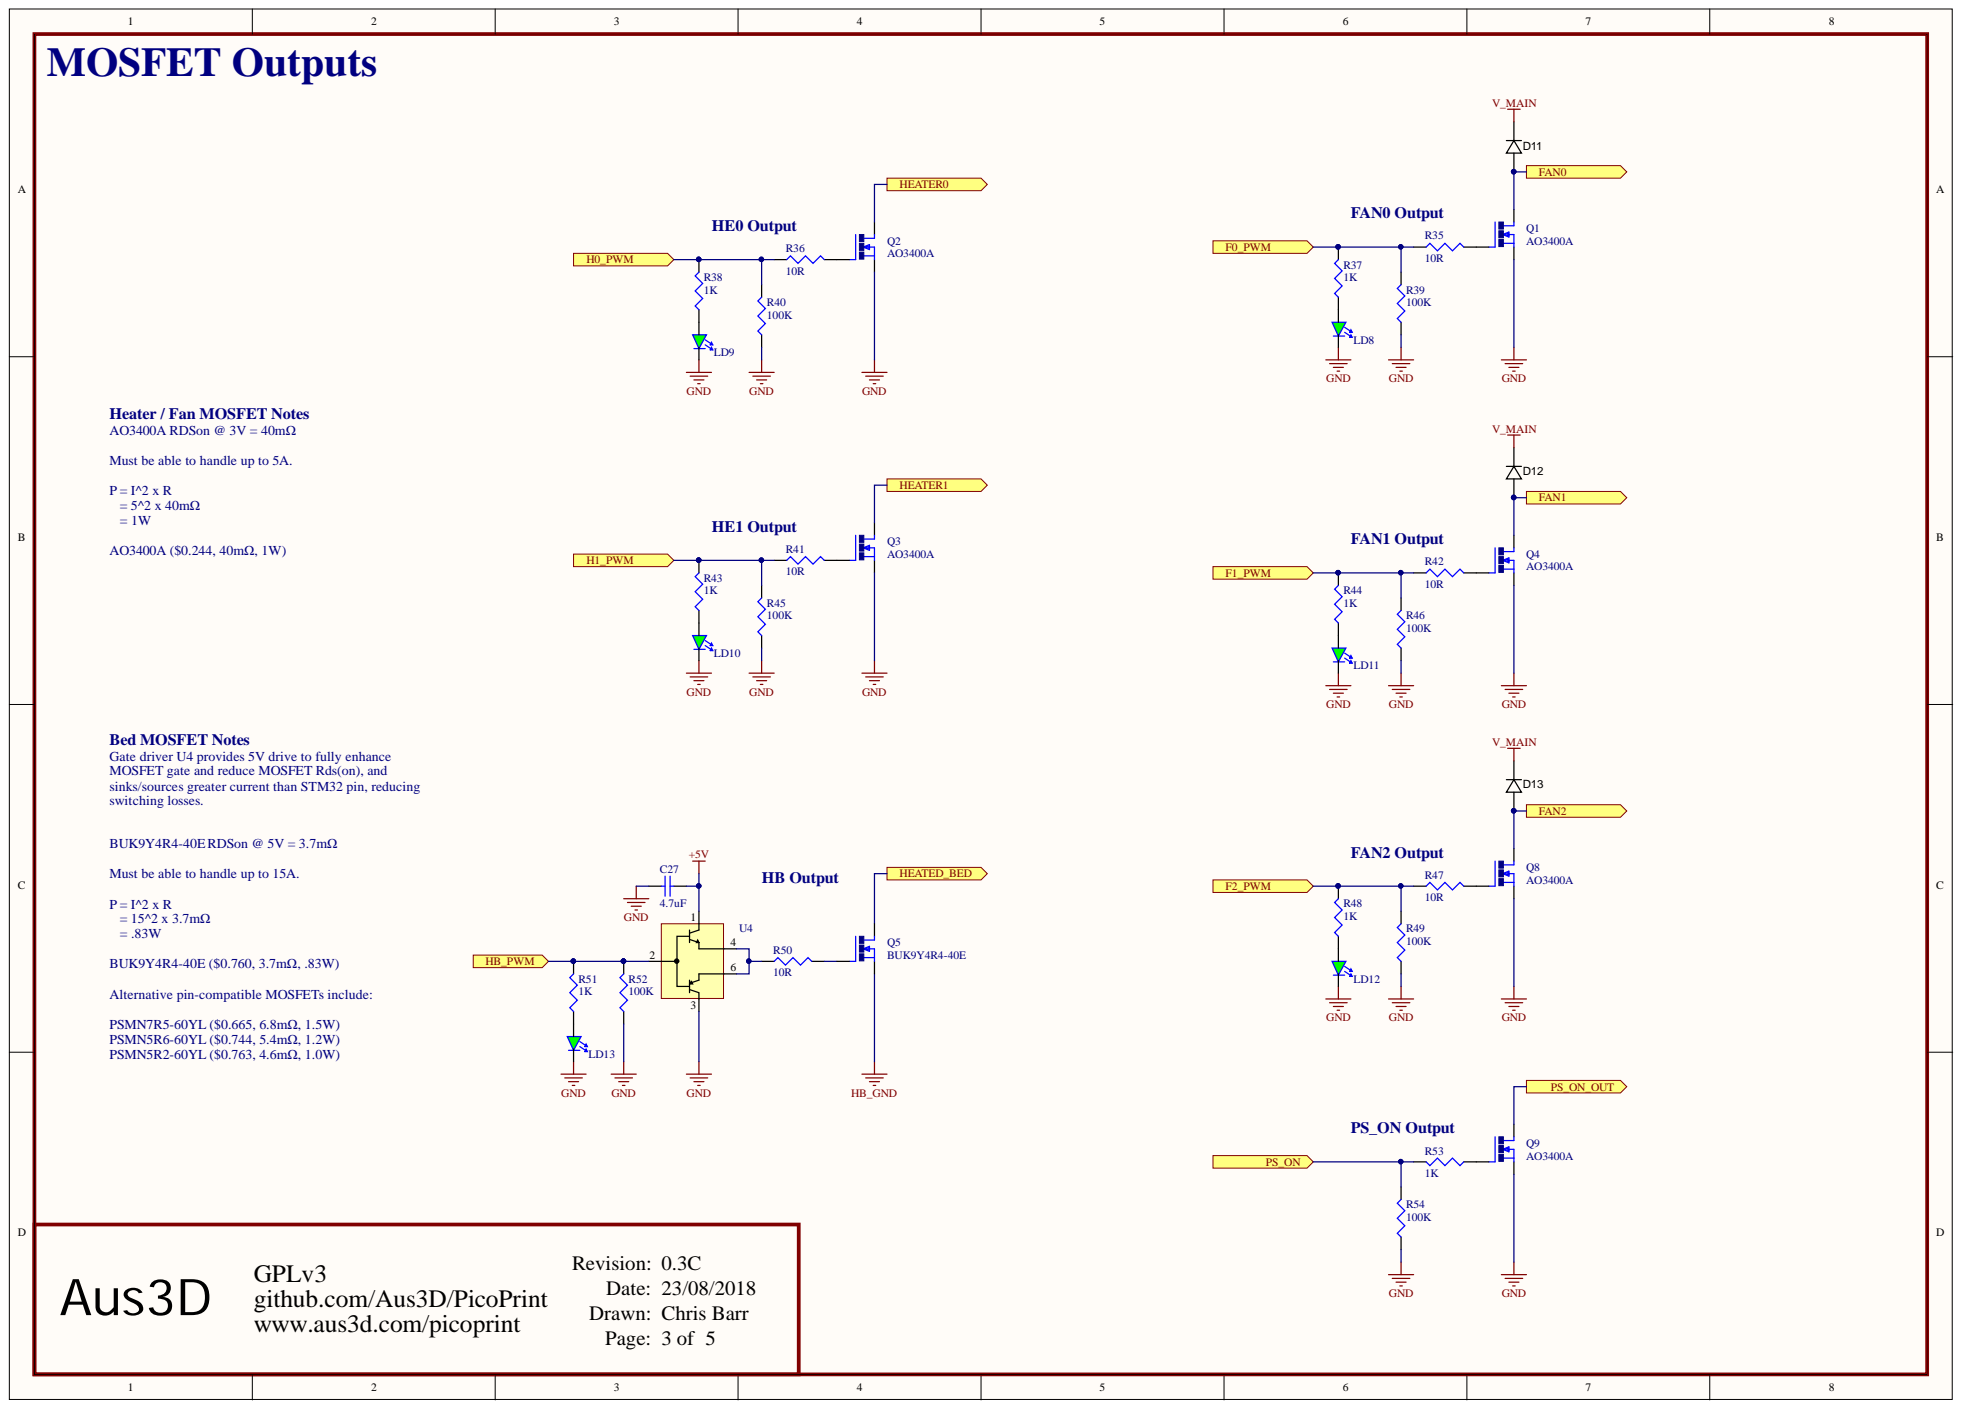
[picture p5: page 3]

Heater / Fan MOSFET Notes
AO3400A RDSon @ 3V = 40mΩ

Must be able to handle up to 5A.

Bed MOSFET Notes
Gate driver U4 provides 5V drive to fully enhance
MOSFET gate and reduce MOSFET Rds(on), and
sinks/sources greater current than STM32 pin, reducing
switching losses.

Must be able to handle up to 15A.

Alternative pin-compatible MOSFETs include:

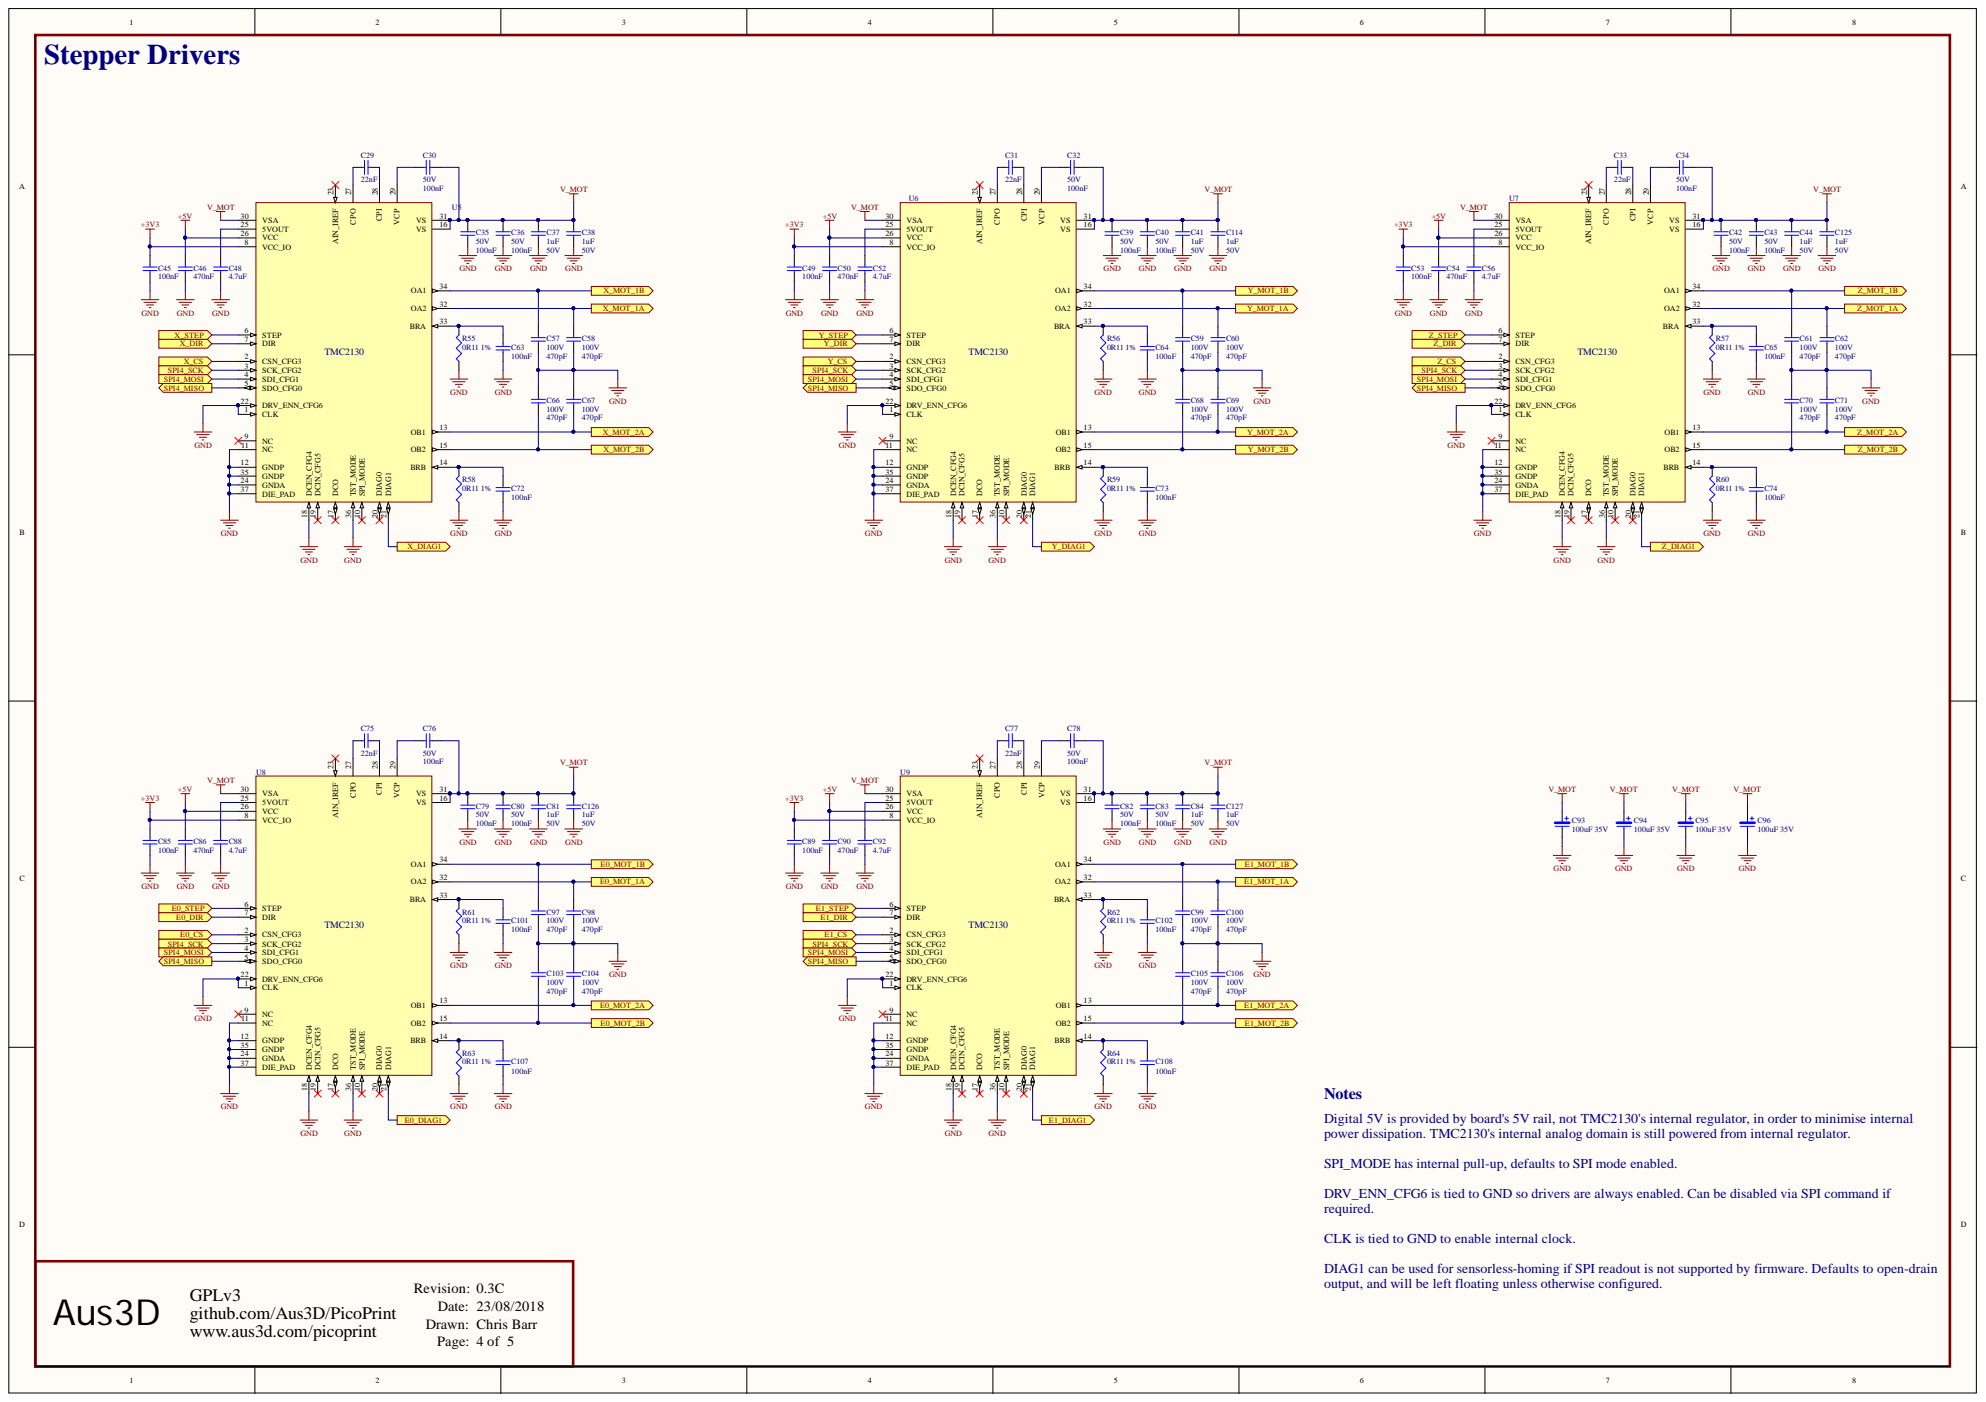
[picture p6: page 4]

Digital 5V is provided by board's 5V rail, not TMC2130's internal regulator, in order to minimise internal
power dissipation. TMC2130's internal analog domain is still powered from internal regulator.

SPI_MODE has internal pull-up, defaults to SPI mode enabled.

DRV_ENN_CFG6 is tied to GND so drivers are always enabled. Can be disabled via SPI command if
required.

CLK is tied to GND to enable internal clock.

DIAG1 can be used for sensorless-homing if SPI readout is not supported by firmware. Defaults to open-drain
output, and will be left floating unless otherwise configured.

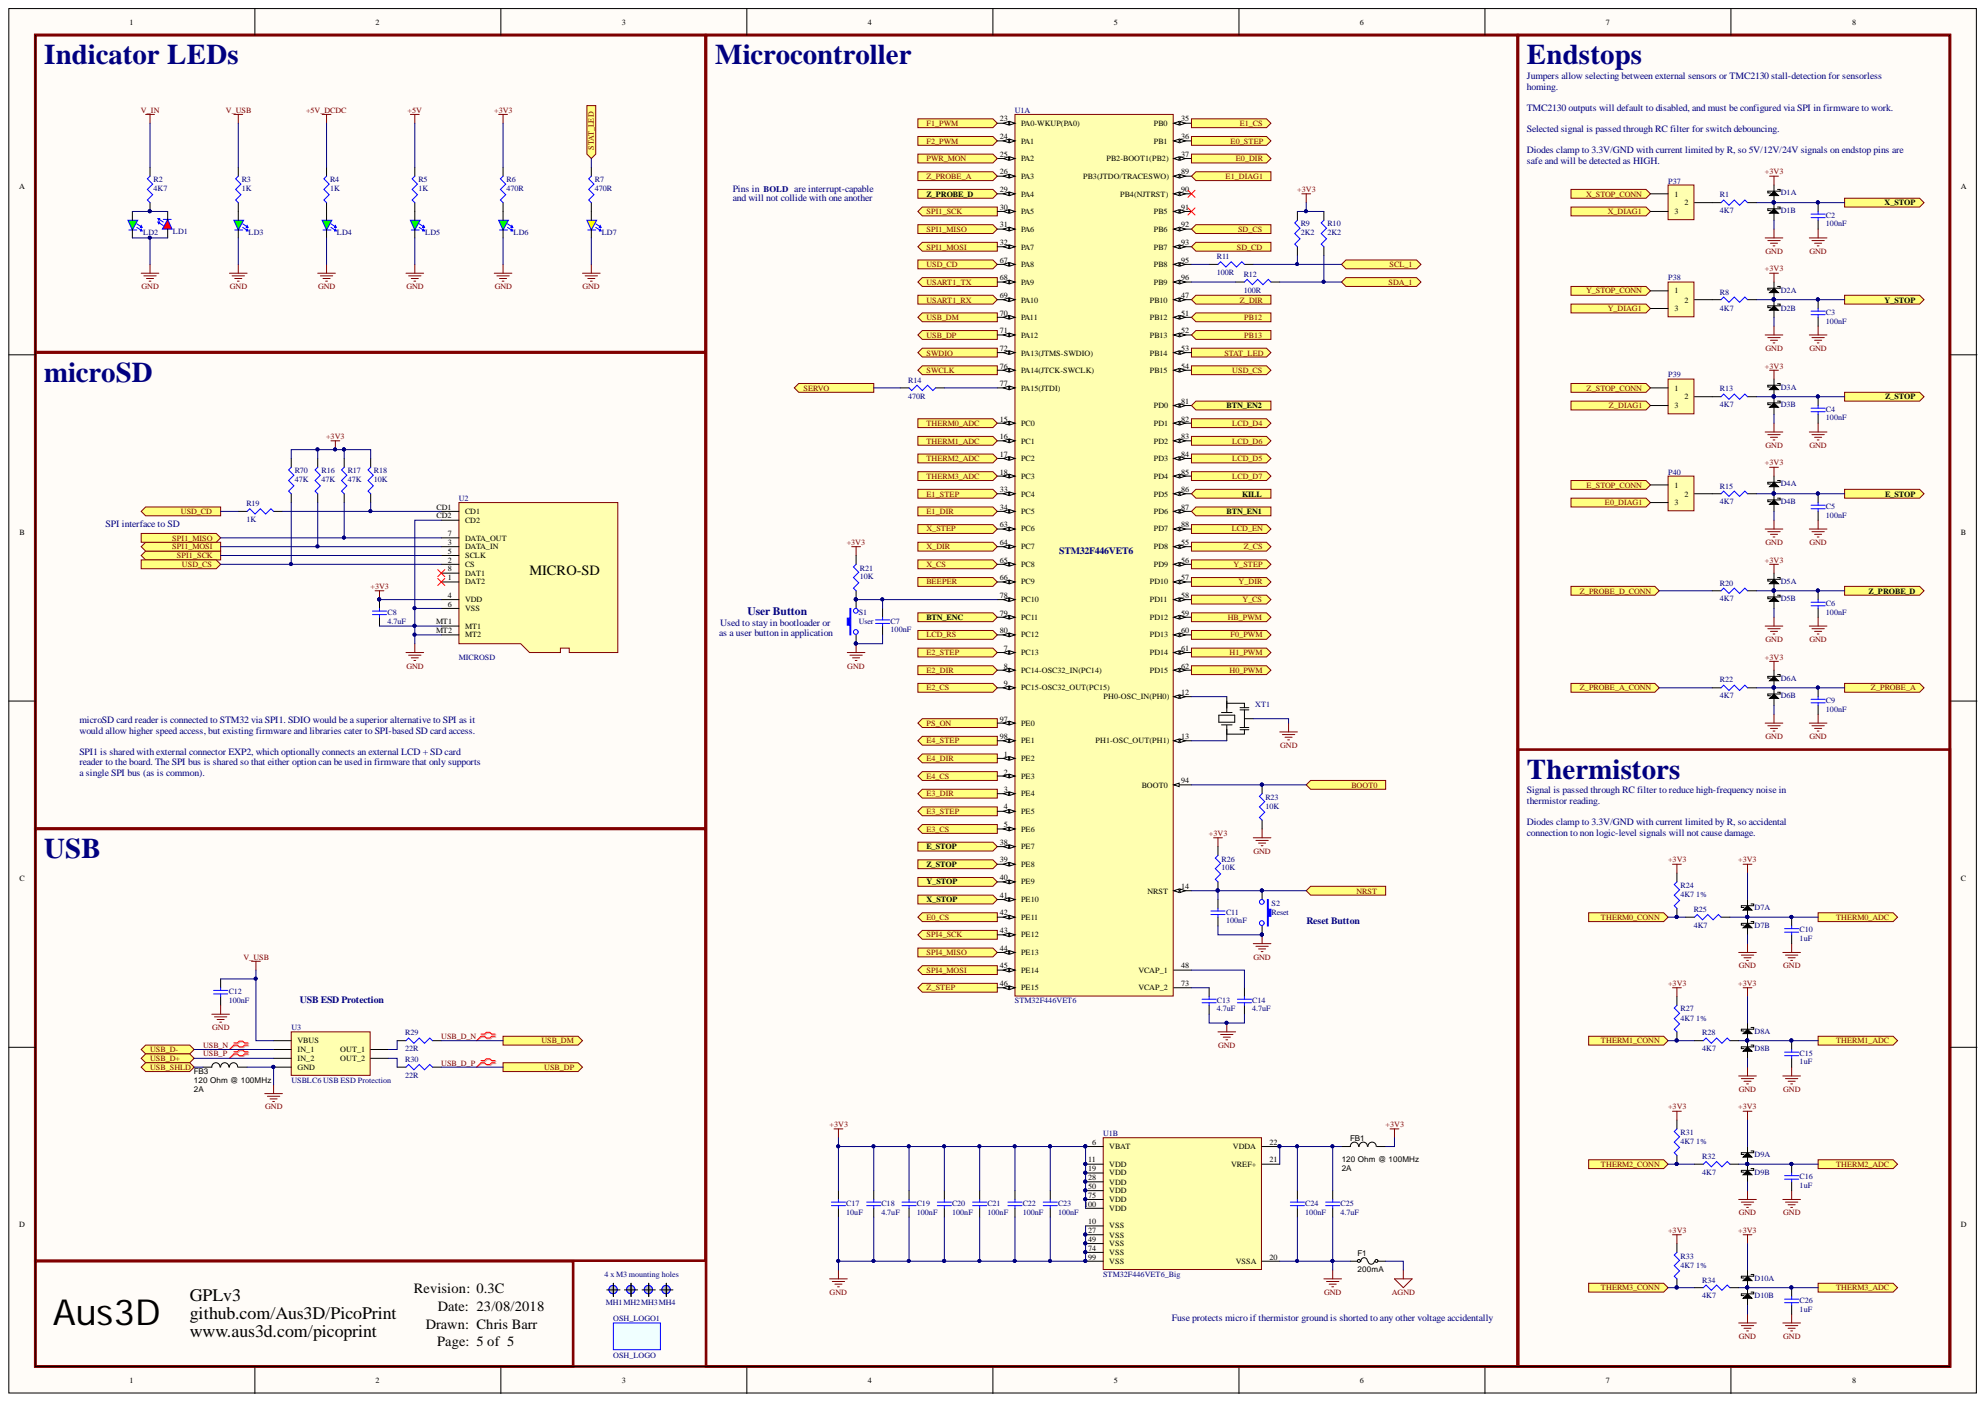
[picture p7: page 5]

Jumpers allow selecting between external sensors or TMC2130 stall-detection for sensorless
homing.

TMC2130 outputs will default to disabled, and must be configured via SPI in firmware to work.

Selected signal is passed through RC filter for switch debouncing.

Diodes clamp to 3.3V/GND with current limited by R, so 5V/12V/24V signals on endstop pins are
safe and will be detected as HIGH.

Pins in BOLD are interrupt-capable and will not collide with one another

SPI interface to SD

Used to stay in bootloader or
as a user button in application

microSD card reader is connected to STM32 via SPI1. SDIO would be a superior alternative to SPI as it
would allow higher speed access, but existing firmware and libraries cater to SPI-based SD card access.

SPI1 is shared with external connector EXP2, which optionally connects an external LCD + SD card
reader to the board. The SPI bus is shared so that either option can be used in firmware that only supports
a single SPI bus (as is common).

Signal is passed through RC filter to reduce high-frequency noise in
thermistor reading.

Diodes clamp to 3.3V/GND with current limited by R, so accidental
connection to non logic-level signals will not cause damage.

Fuse protects micro if thermistor ground is shorted to any other voltage accidentally

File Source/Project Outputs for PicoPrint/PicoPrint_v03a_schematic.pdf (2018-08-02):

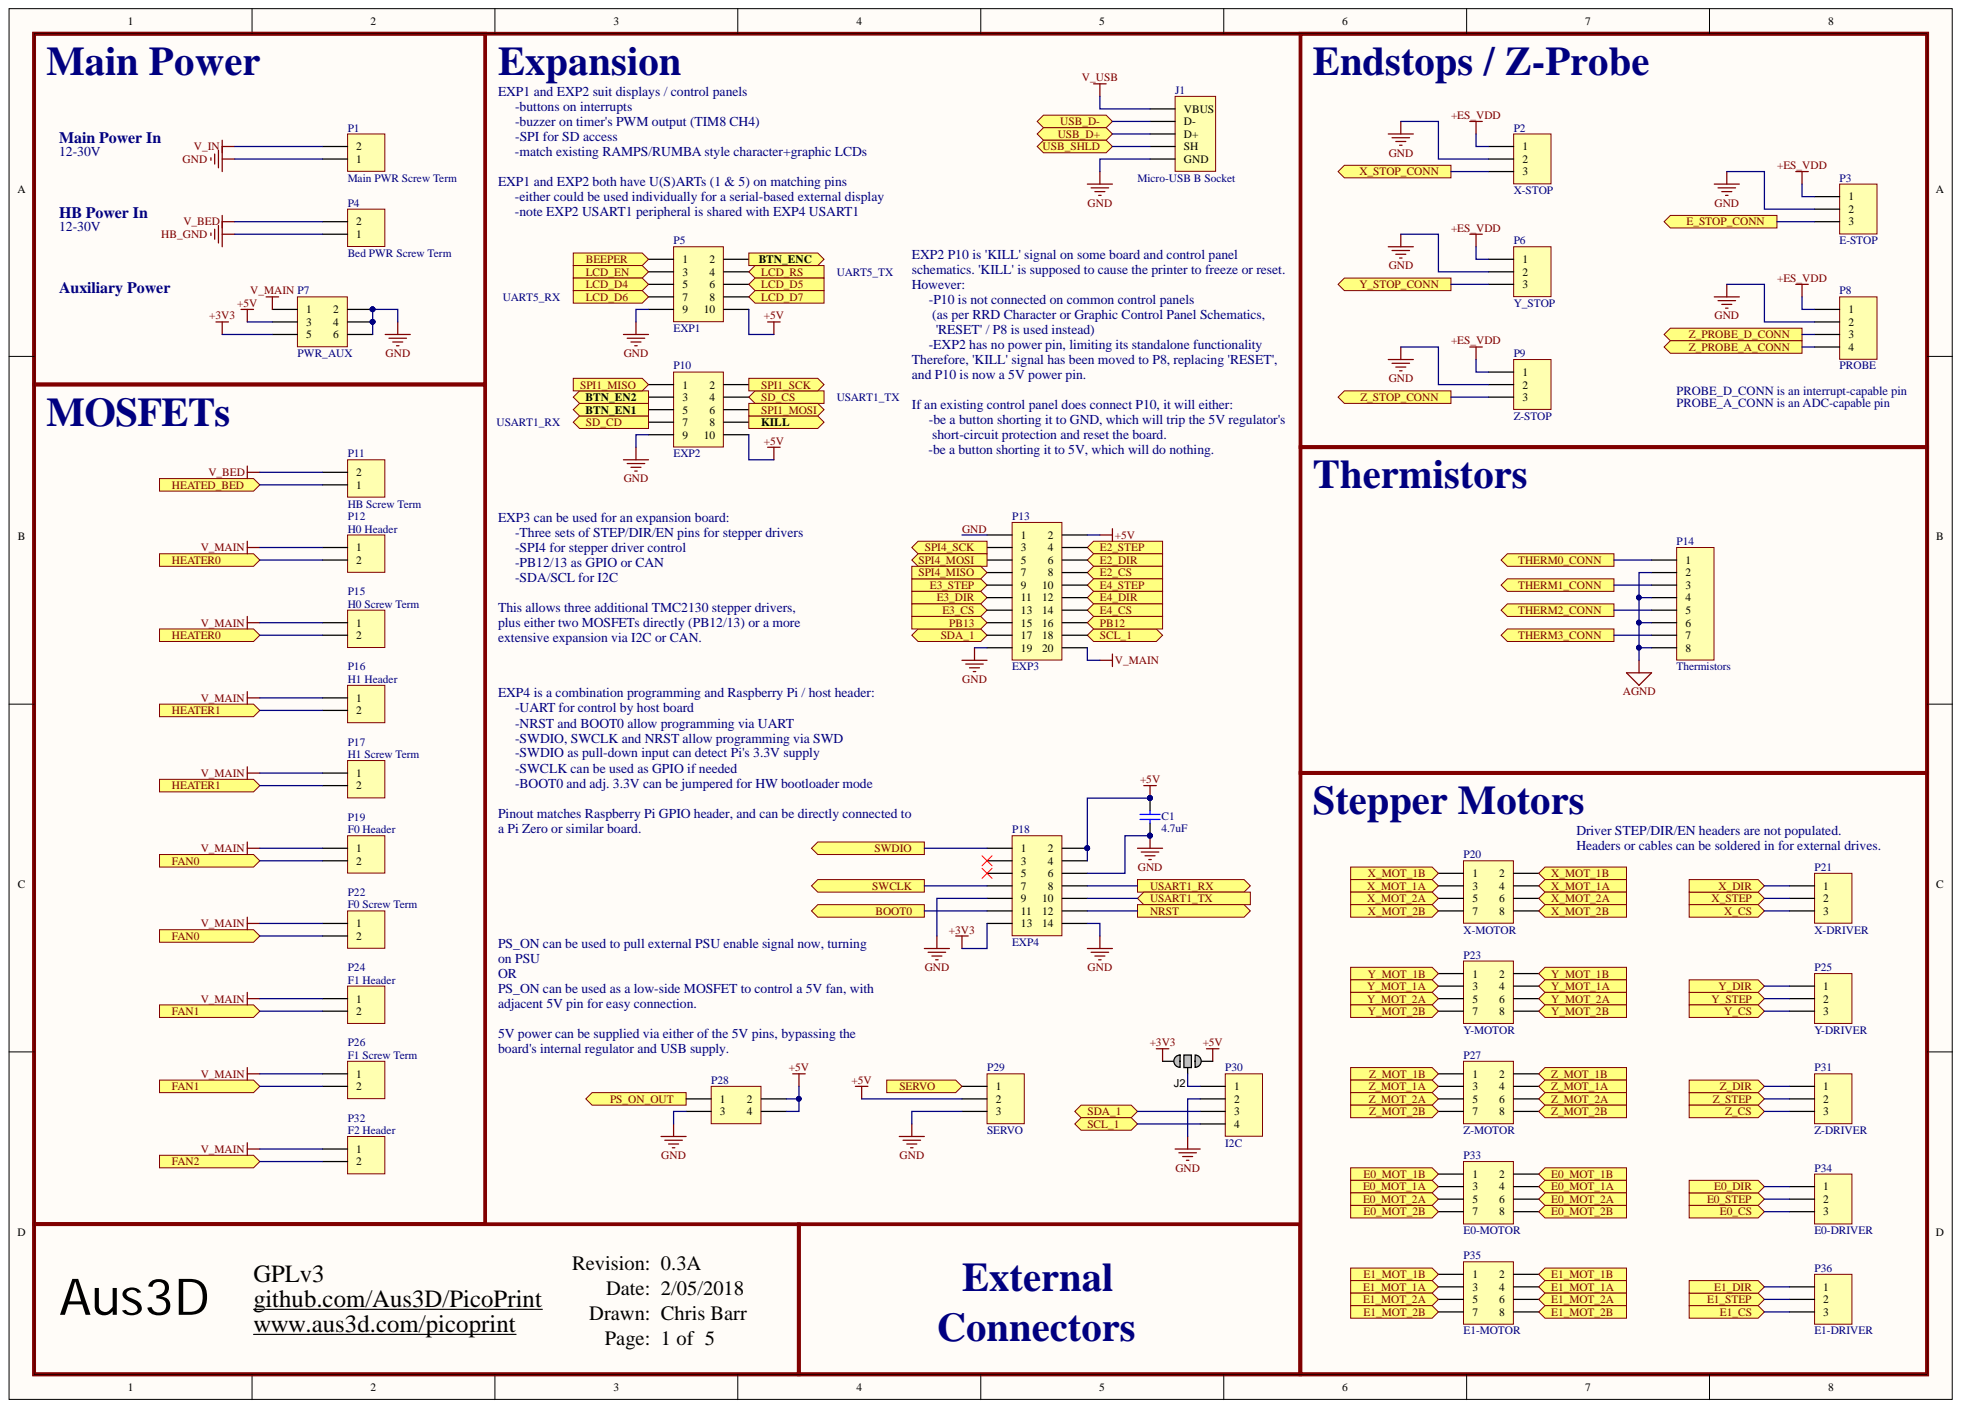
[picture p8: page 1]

EXP1 and EXP2 suit displays / control panels
-buttons on interrupts
-buzzer on timer's PWM output (TIM8 CH4)
-SPI for SD access
-match existing RAMPS/RUMBA style character+graphic LCDs

EXP1 and EXP2 both have U(S)ARTs (1 & 5) on matching pins
-either could be used individually for a serial-based external display
-note EXP2 USART1 peripheral is shared with EXP4 USART1

EXP2 P10 is 'KILL' signal on some board and control panel
schematics. 'KILL' is supposed to cause the printer to freeze or reset.
However:
-P10 is not connected on common control panels
(as per RRD Character or Graphic Control Panel Schematics,
'RESET' / P8 is used instead)
-EXP2 has no power pin, limiting its standalone functionality
Therefore, 'KILL' signal has been moved to P8, replacing 'RESET',
and P10 is now a 5V power pin.

PROBE_D_CONN is an interrupt-capable pin
PROBE_A_CONN is an ADC-capable pin

If an existing control panel does connect P10, it will either:
-be a button shorting it to GND, which will trip the 5V regulator's
short-circuit protection and reset the board.
-be a button shorting it to 5V, which will do nothing.

EXP3 can be used for an expansion board:
-Three sets of STEP/DIR/EN pins for stepper drivers
-SPI4 for stepper driver control
-PB12/13 as GPIO or CAN
-SDA/SCL for I2C

This allows three additional TMC2130 stepper drivers,
plus either two MOSFETs directly (PB12/13) or a more
extensive expansion via I2C or CAN.

EXP4 is a combination programming and Raspberry Pi / host header:
-UART for control by host board
-NRST and BOOT0 allow programming via UART
-SWDIO, SWCLK and NRST allow programming via SWD
-SWDIO as pull-down input can detect Pi's 3.3V supply
-SWCLK can be used as GPIO if needed
-BOOT0 and adj. 3.3V can be jumpered for HW bootloader mode

Pinout matches Raspberry Pi GPIO header, and can be directly connected to
a Pi Zero or similar board.

Driver STEP/DIR/EN headers are not populated.
Headers or cables can be soldered in for external drives.

PS_ON can be used to pull external PSU enable signal now, turning
on PSU
PS_ON can be used as a low-side MOSFET to control a 5V fan, with
adjacent 5V pin for easy connection.

5V power can be supplied via either of the 5V pins, bypassing the
board's internal regulator and USB supply.

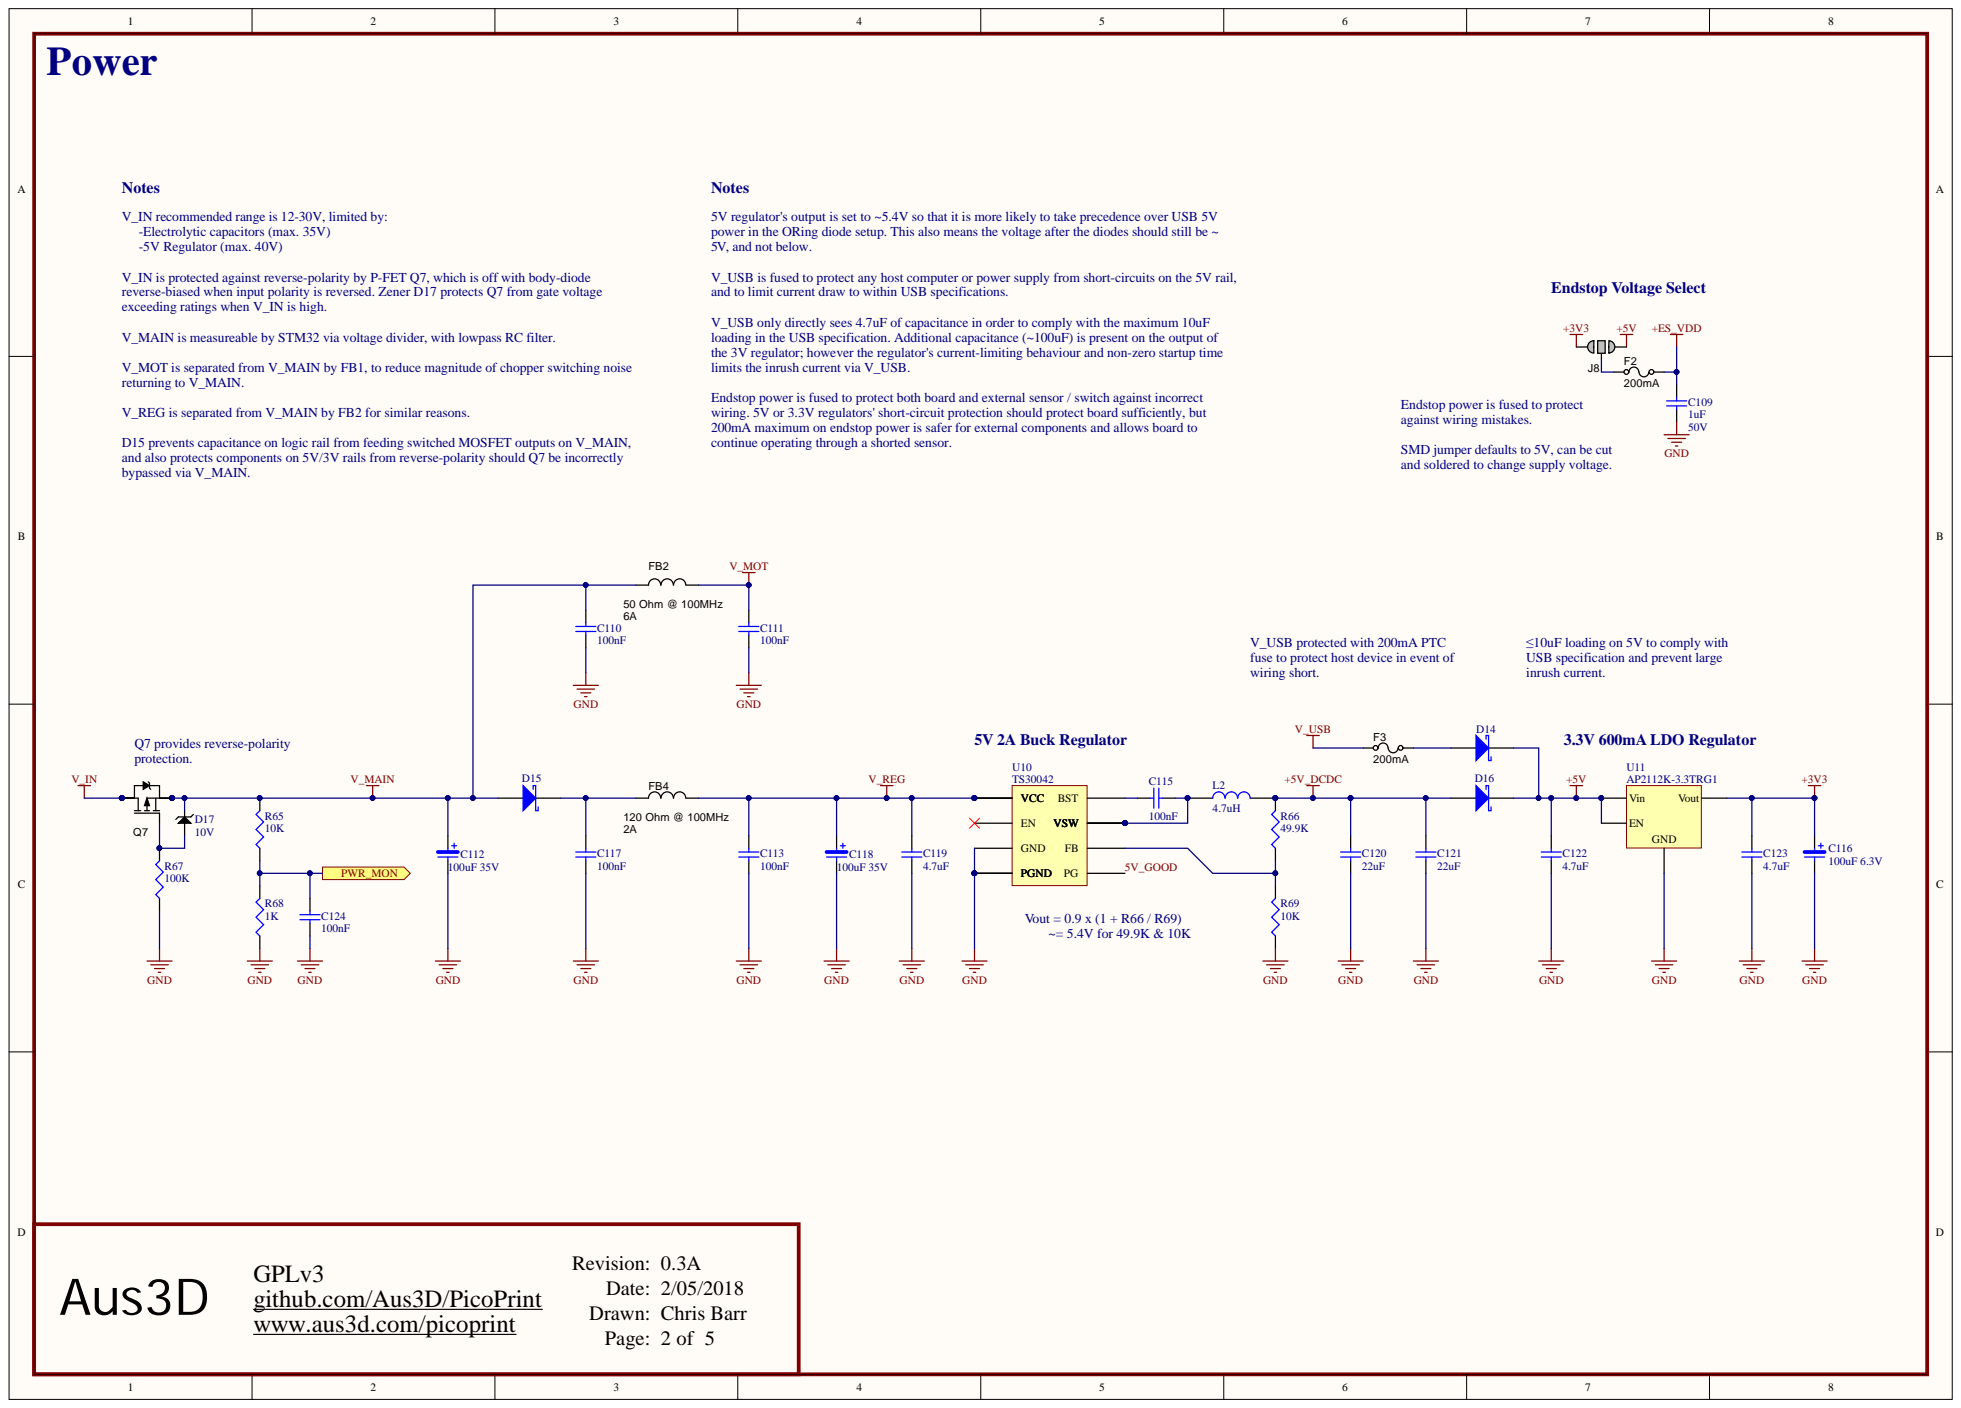
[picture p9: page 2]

V_IN recommended range is 12-30V, limited by:
-Electrolytic capacitors (max. 35V)
-5V Regulator (max. 40V)

5V regulator's output is set to ~5.4V so that it is more likely to take precedence over USB 5V
power in the ORing diode setup. This also means the voltage after the diodes should still be ~
5V, and not below.

V_IN is protected against reverse-polarity by P-FET Q7, which is off with body-diode
reverse-biased when input polarity is reversed. Zener D17 protects Q7 from gate voltage
exceeding ratings when V_IN is high.

V_USB is fused to protect any host computer or power supply from short-circuits on the 5V rail,
and to limit current draw to within USB specifications.

V_USB only directly sees 4.7uF of capacitance in order to comply with the maximum 10uF
loading in the USB specification. Additional capacitance (~100uF) is present on the output of
the 3V regulator; however the regulator's current-limiting behaviour and non-zero startup time
limits the inrush current via V_USB.

V_MAIN is measureable by STM32 via voltage divider, with lowpass RC filter.

V_MOT is separated from V_MAIN by FB1, to reduce magnitude of chopper switching noise
returning to V_MAIN.

Endstop power is fused to protect both board and external sensor / switch against incorrect
wiring. 5V or 3.3V regulators' short-circuit protection should protect board sufficiently, but
200mA maximum on endstop power is safer for external components and allows board to
continue operating through a shorted sensor.

Endstop power is fused to protect
against wiring mistakes.

V_REG is separated from V_MAIN by FB2 for similar reasons.

D15 prevents capacitance on logic rail from feeding switched MOSFET outputs on V_MAIN,
and also protects components on 5V/3V rails from reverse-polarity should Q7 be incorrectly
bypassed via V_MAIN.

SMD jumper defaults to 5V, can be cut
and soldered to change supply voltage.

V_USB protected with 200mA PTC
fuse to protect host device in event of
wiring short.

≤10uF loading on 5V to comply with
USB specification and prevent large
inrush current.

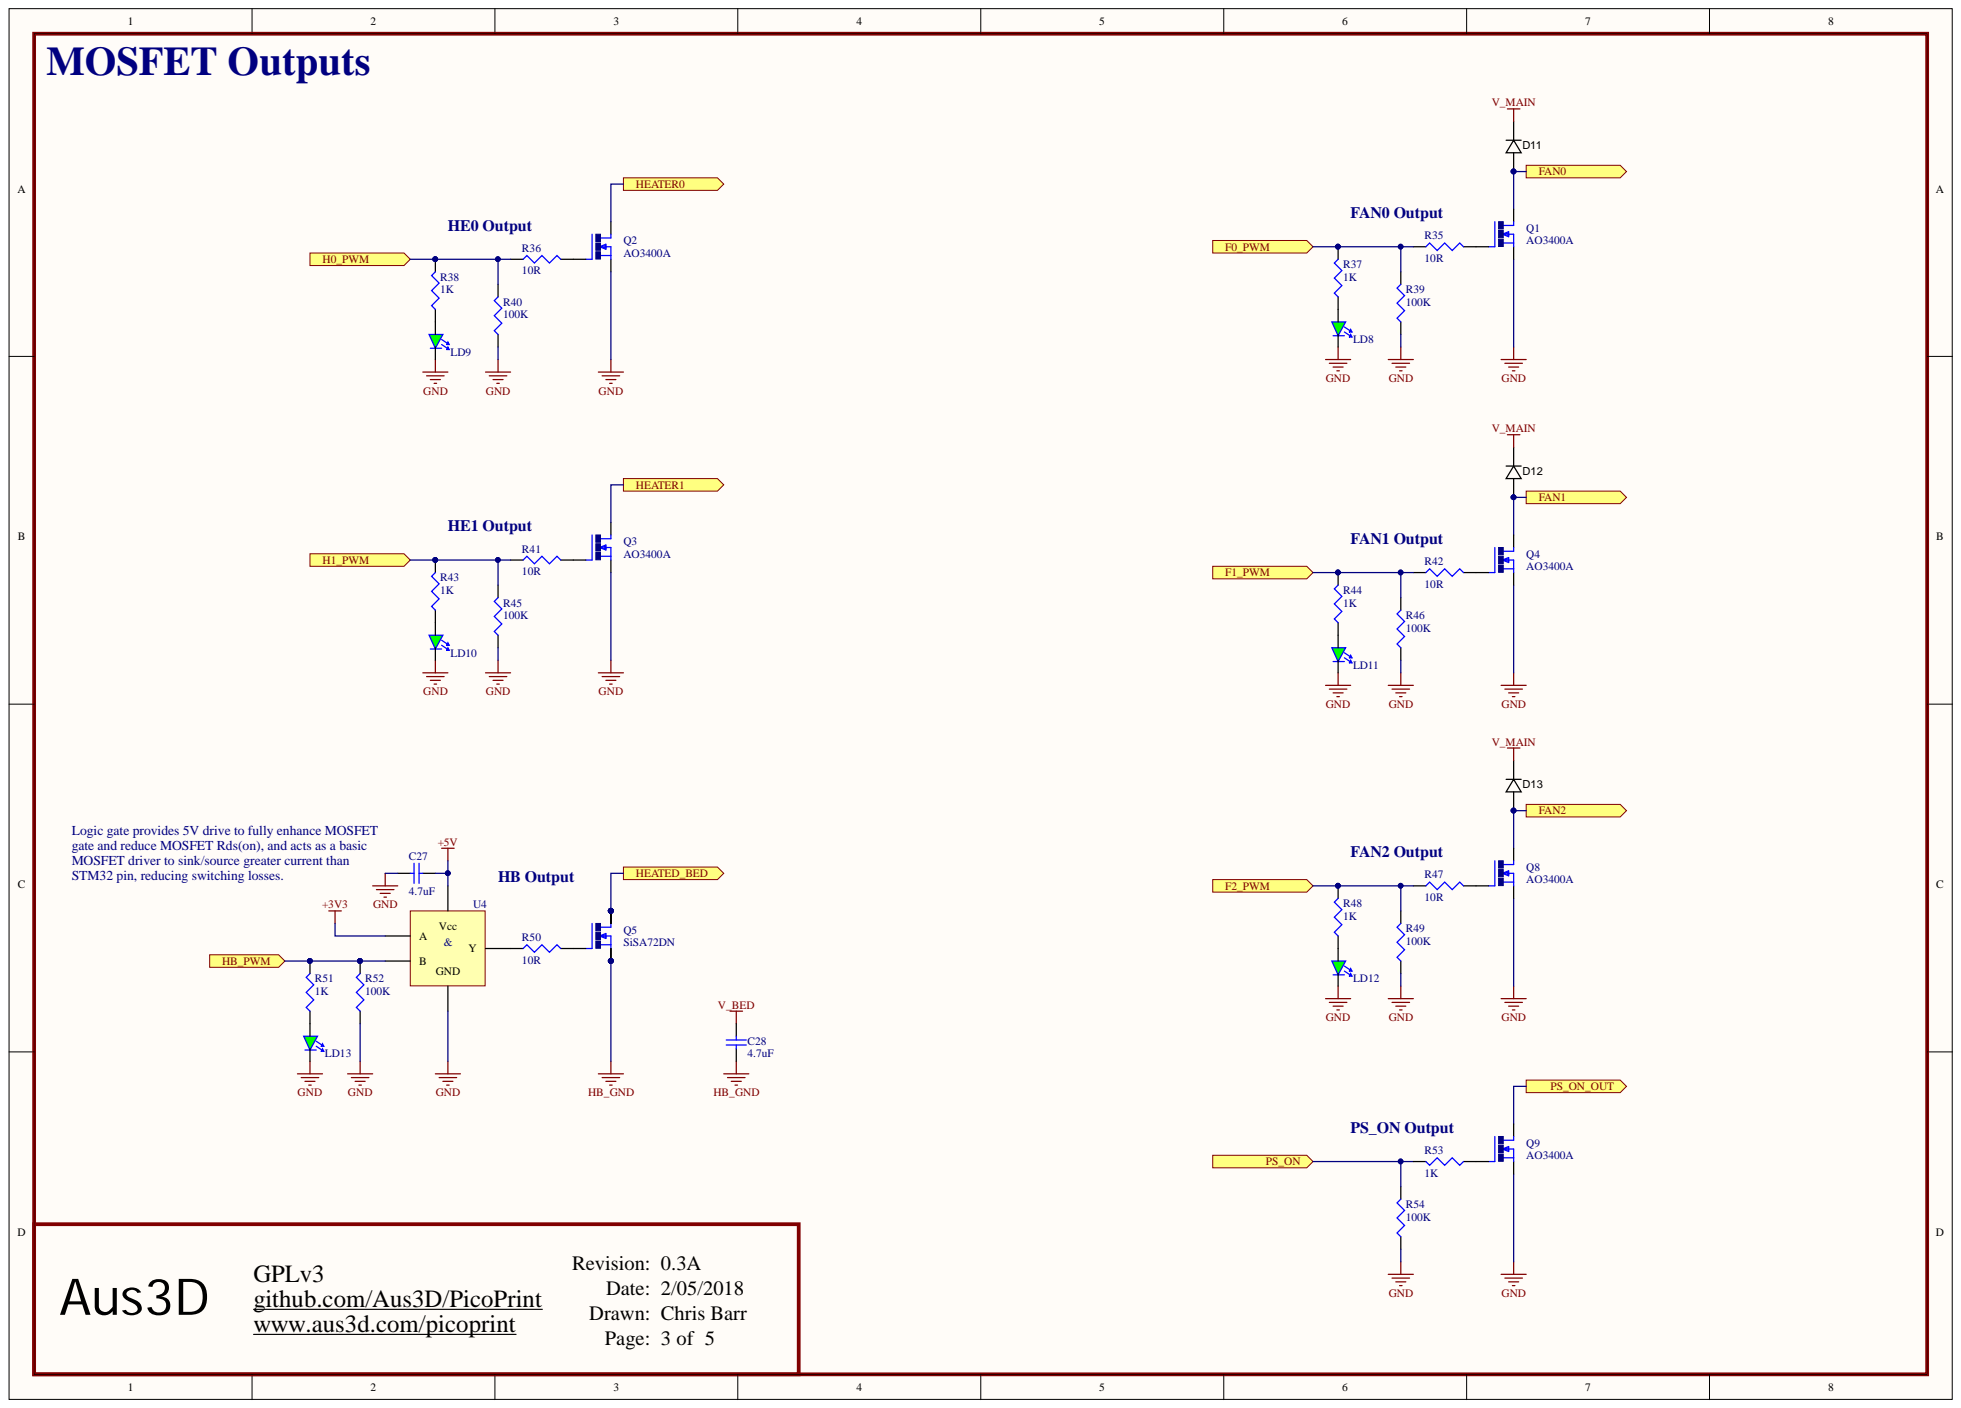
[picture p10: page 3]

Logic gate provides 5V drive to fully enhance M
gate and reduce M
STM32 pin, reducing switching losses.

OSFET Rds(on), and acts as a basic

OSFET driver to sink/source greater current than

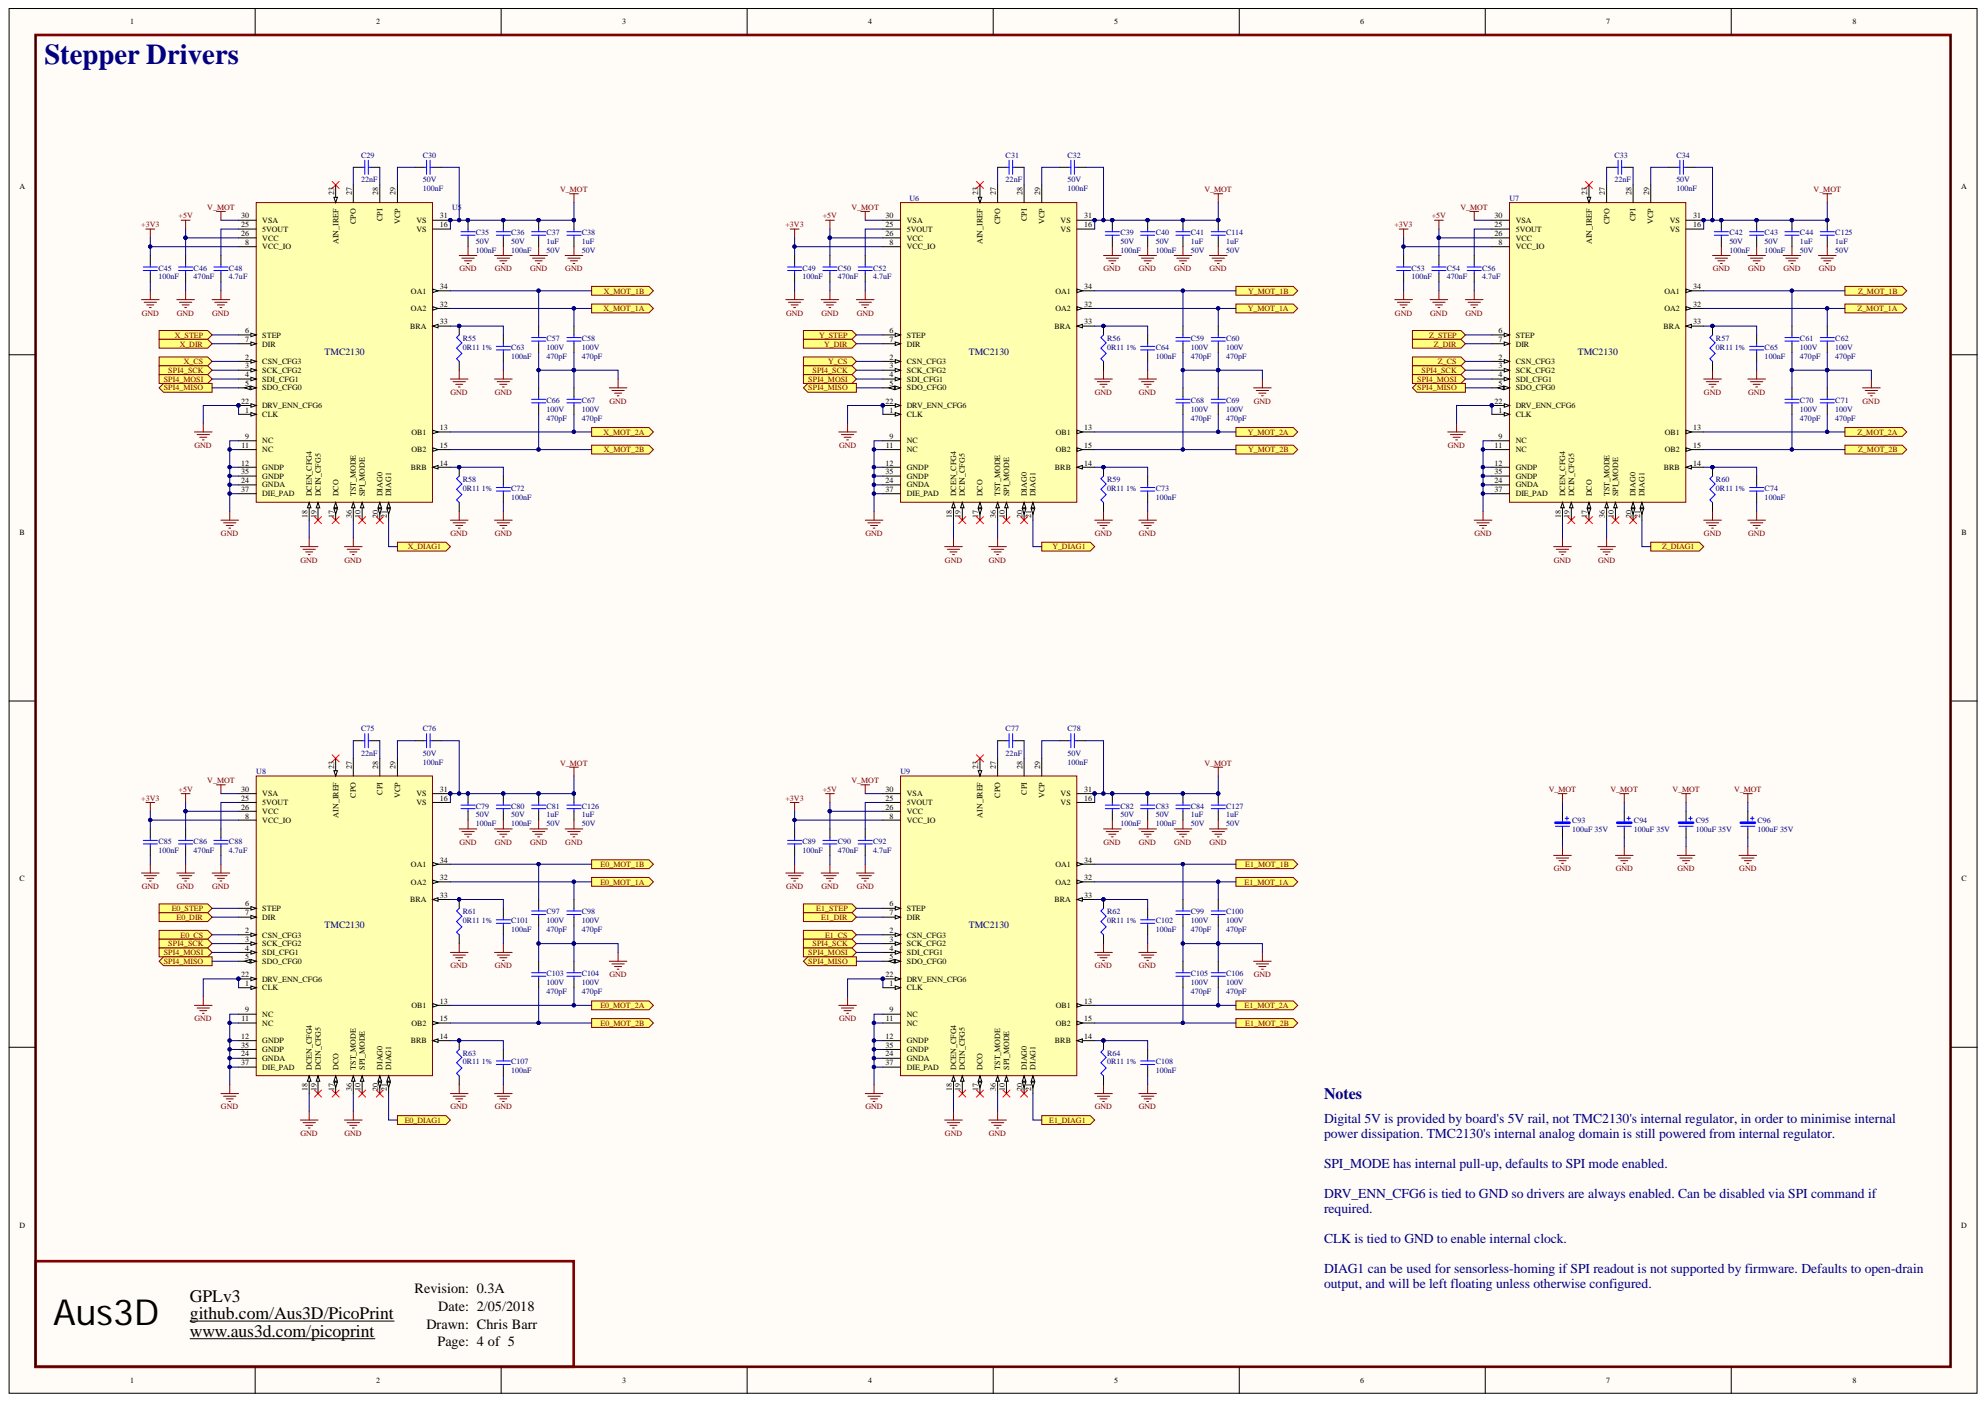
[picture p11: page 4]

Digital 5V is provided by board's 5V rail, not TMC2130's internal regulator, in order to minimise internal
power dissipation. TMC2130's internal analog domain is still powered from internal regulator.

SPI_MODE has internal pull-up, defaults to SPI mode enabled.

DRV_ENN_CFG6 is tied to GND so drivers are always enabled. Can be disabled via SPI command if
required.

CLK is tied to GND to enable internal clock.

DIAG1 can be used for sensorless-homing if SPI readout is not supported by firmware. Defaults to open-drain
output, and will be left floating unless otherwise configured.

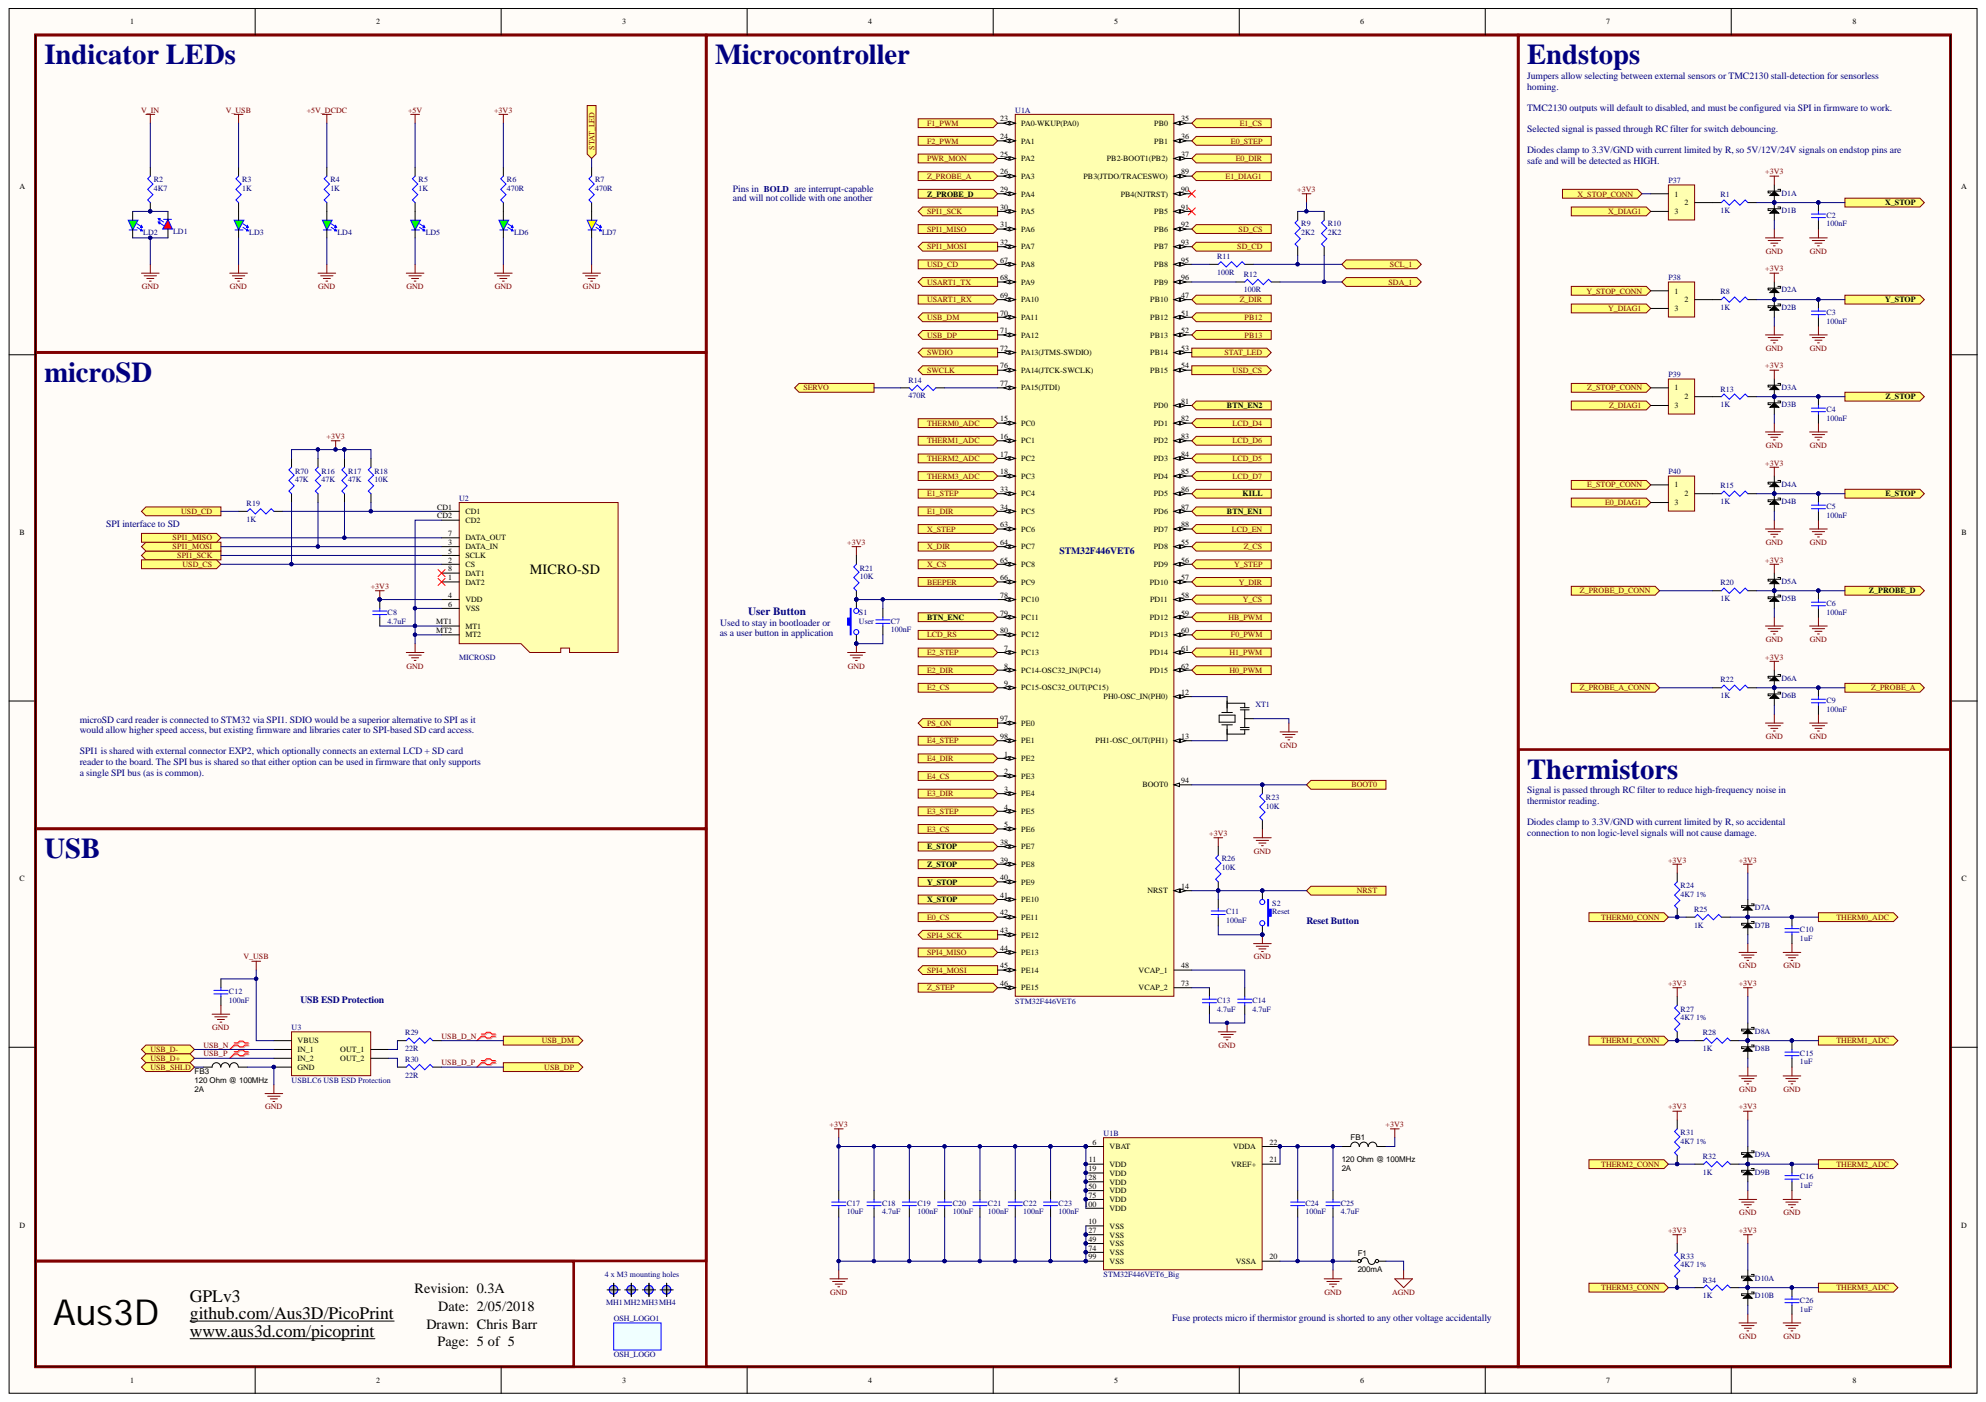
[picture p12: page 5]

Jumpers allow selecting between external sensors or TMC2130 stall-detection for sensorless
homing.

TMC2130 outputs will default to disabled, and must be configured via SPI in firmware to work.

Selected signal is passed through RC filter for switch debouncing.

Diodes clamp to 3.3V/GND with current limited by R, so 5V/12V/24V signals on endstop pins are
safe and will be detected as HIGH.

Pins in BOLD are interrupt-capable and will not collide with one another

SPI interface to SD

Used to stay in bootloader or
as a user button in application

microSD card reader is connected to STM32 via SPI1. SDIO would be a superior alternative to SPI as it
would allow higher speed access, but existing firmware and libraries cater to SPI-based SD card access.

SPI1 is shared with external connector EXP2, which optionally connects an external LCD + SD card
reader to the board. The SPI bus is shared so that either option can be used in firmware that only supports
a single SPI bus (as is common).

Signal is passed through RC filter to reduce high-frequency noise in
thermistor reading.

Diodes clamp to 3.3V/GND with current limited by R, so accidental
connection to non logic-level signals will not cause damage.

Fuse protects micro if thermistor ground is shorted to any other voltage accidentally

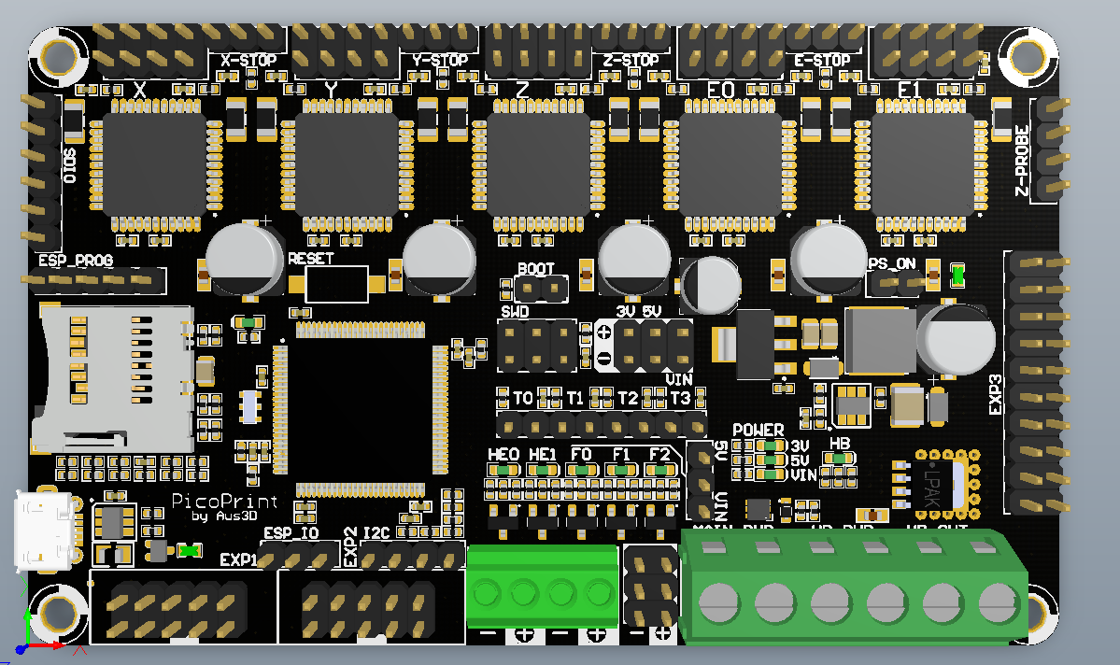
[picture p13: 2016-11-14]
Source/Project Outputs for PicoPrint/PicoPrint_v01a_render.PNG

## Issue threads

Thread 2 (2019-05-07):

Replace MOSFET Driver

chrissbarr, 2019-05-07:
Same issue as Aus3D/RUMBA32#6, MOSFET driver should be replaced with a part that actually changes the voltage level.

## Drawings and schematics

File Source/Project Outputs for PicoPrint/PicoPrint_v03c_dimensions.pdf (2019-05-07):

104.00mm

110.00mm

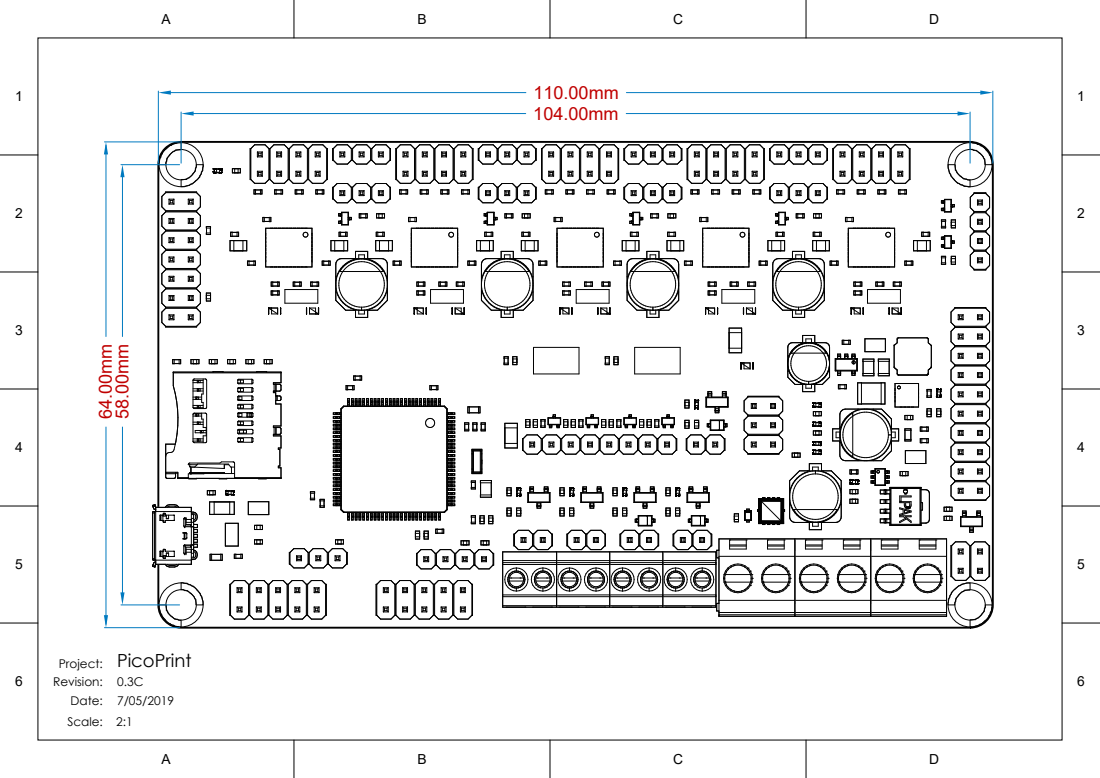
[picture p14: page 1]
Scale: 2:1; Date: 7/05/2019; Revision: 0.3C; Project: PicoPrint

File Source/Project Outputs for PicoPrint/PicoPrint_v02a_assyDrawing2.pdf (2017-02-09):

A

B

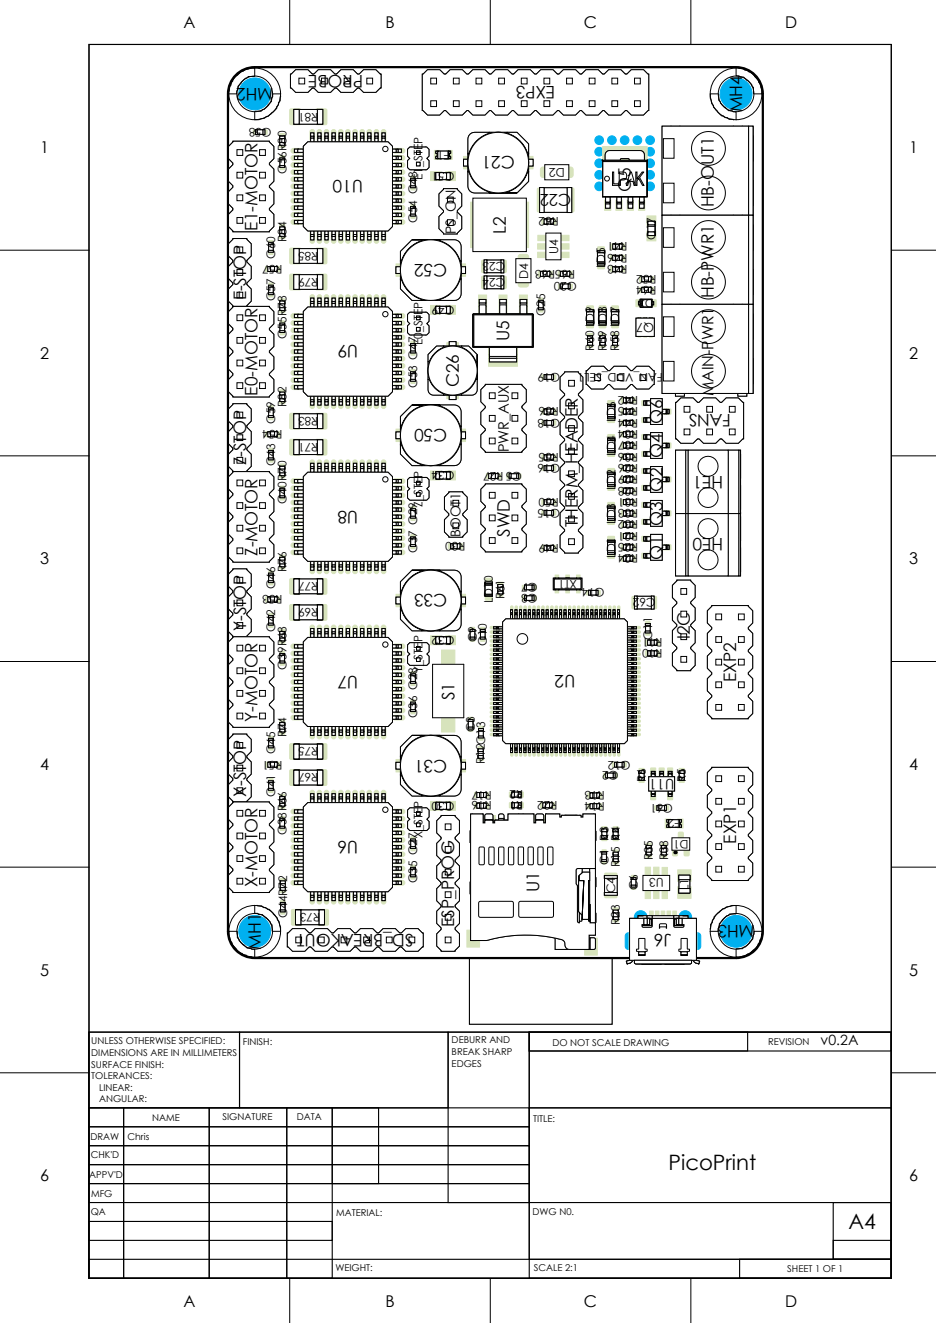
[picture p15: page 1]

E1-MOTOR E0-MOTOR Z-MOTOR X-MOTOR Y-MOTOR

E-STOP Z-STOP X-STOP Y-STOP

E0-MOTOR Z-MOTOR X-MOTOR Y-MOTOR

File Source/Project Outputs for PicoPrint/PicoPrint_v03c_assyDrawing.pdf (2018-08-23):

A

B

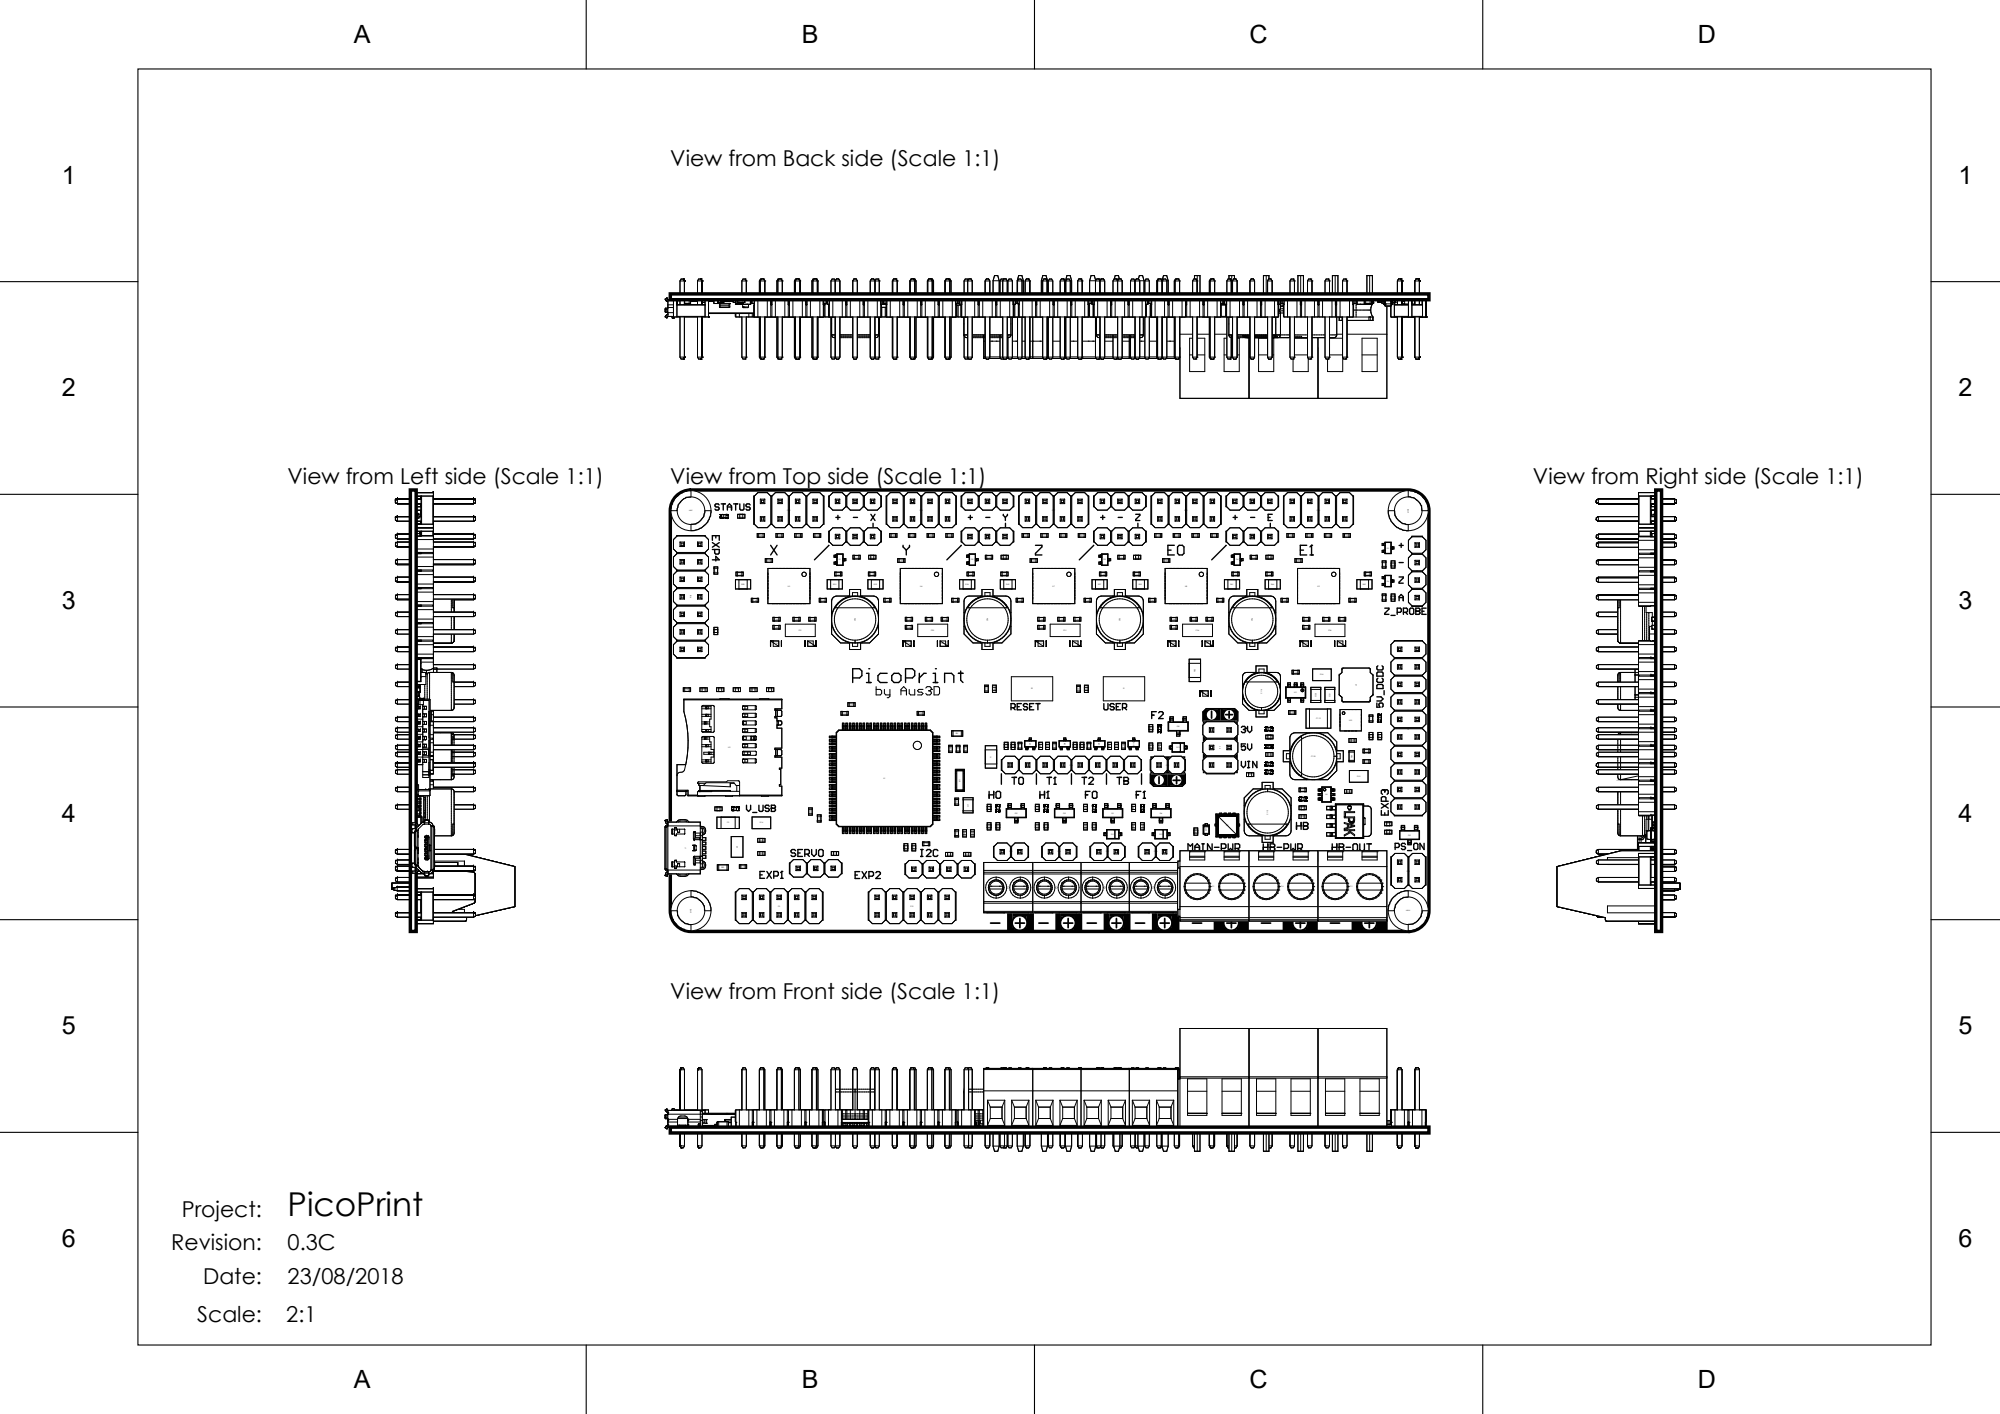
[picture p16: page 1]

View from Back side (Scale 1:1)

View from Top side (Scale 1:1)

View from Front side (Scale 1:1)

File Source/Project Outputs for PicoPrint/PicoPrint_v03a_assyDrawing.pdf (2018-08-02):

A

B

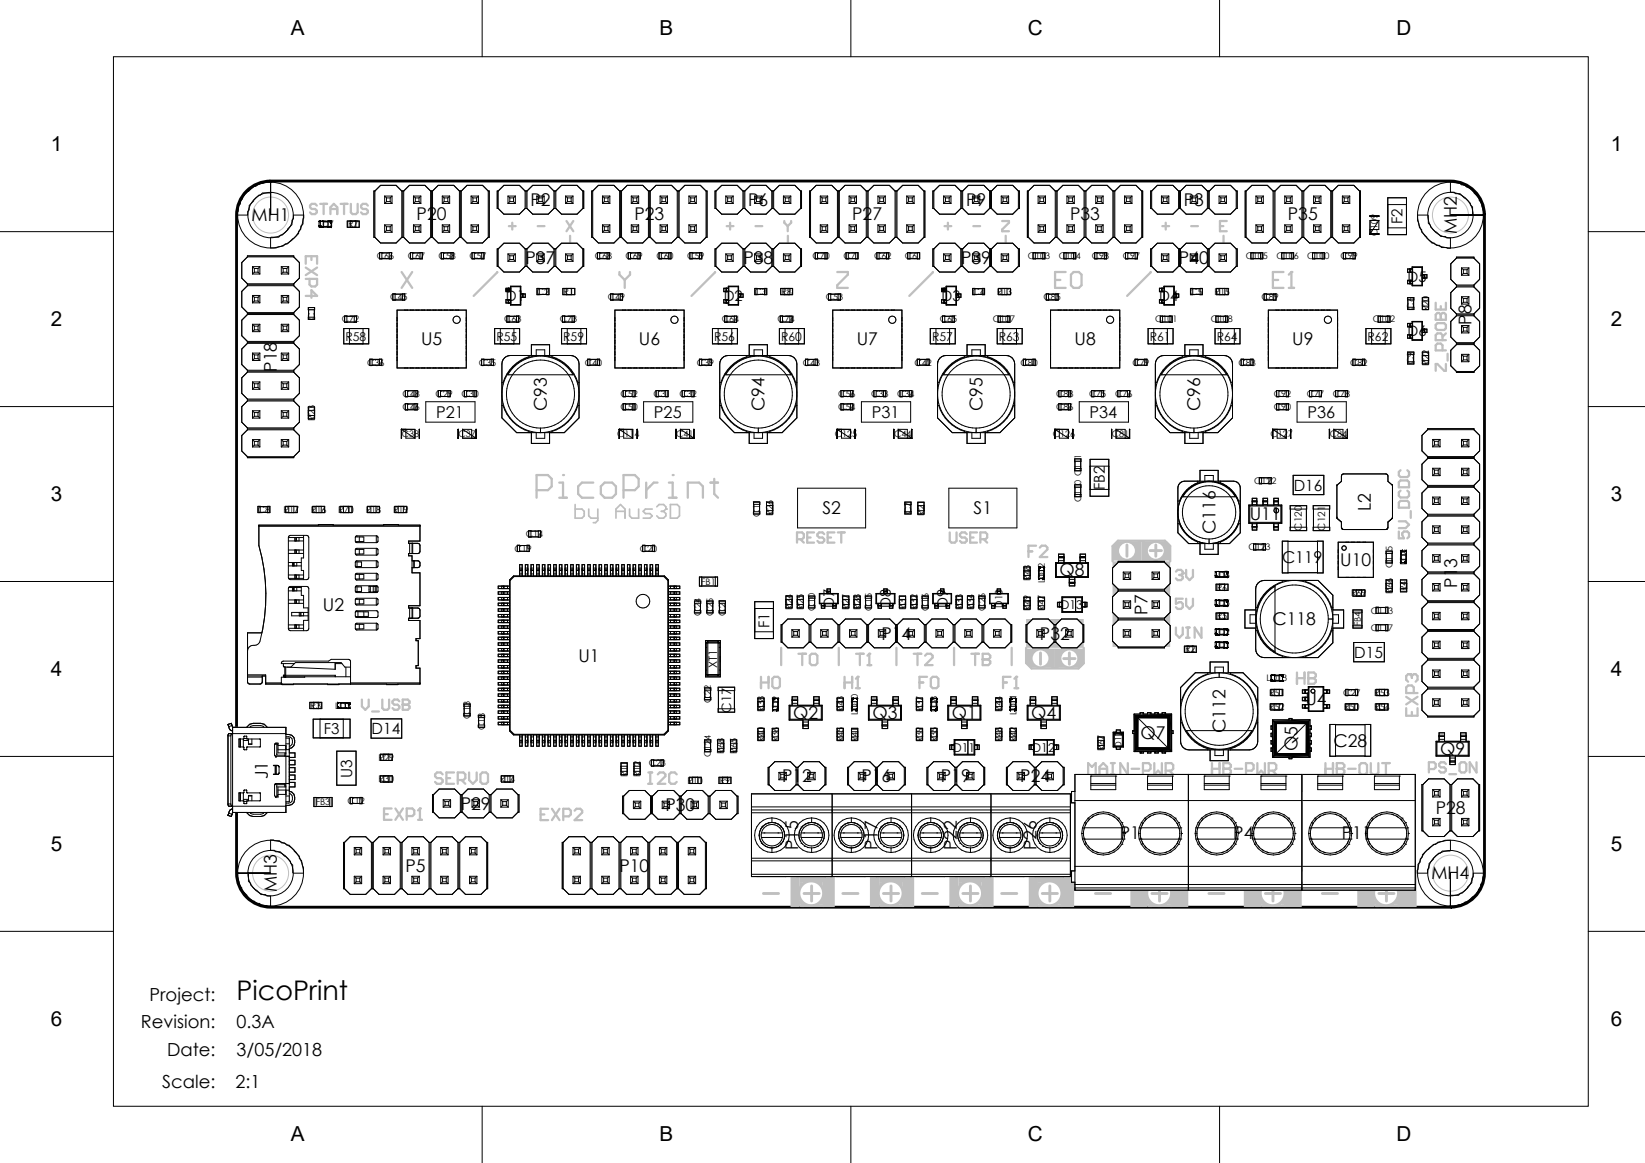
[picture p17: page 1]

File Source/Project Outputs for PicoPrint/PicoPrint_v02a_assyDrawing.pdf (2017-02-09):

A

B

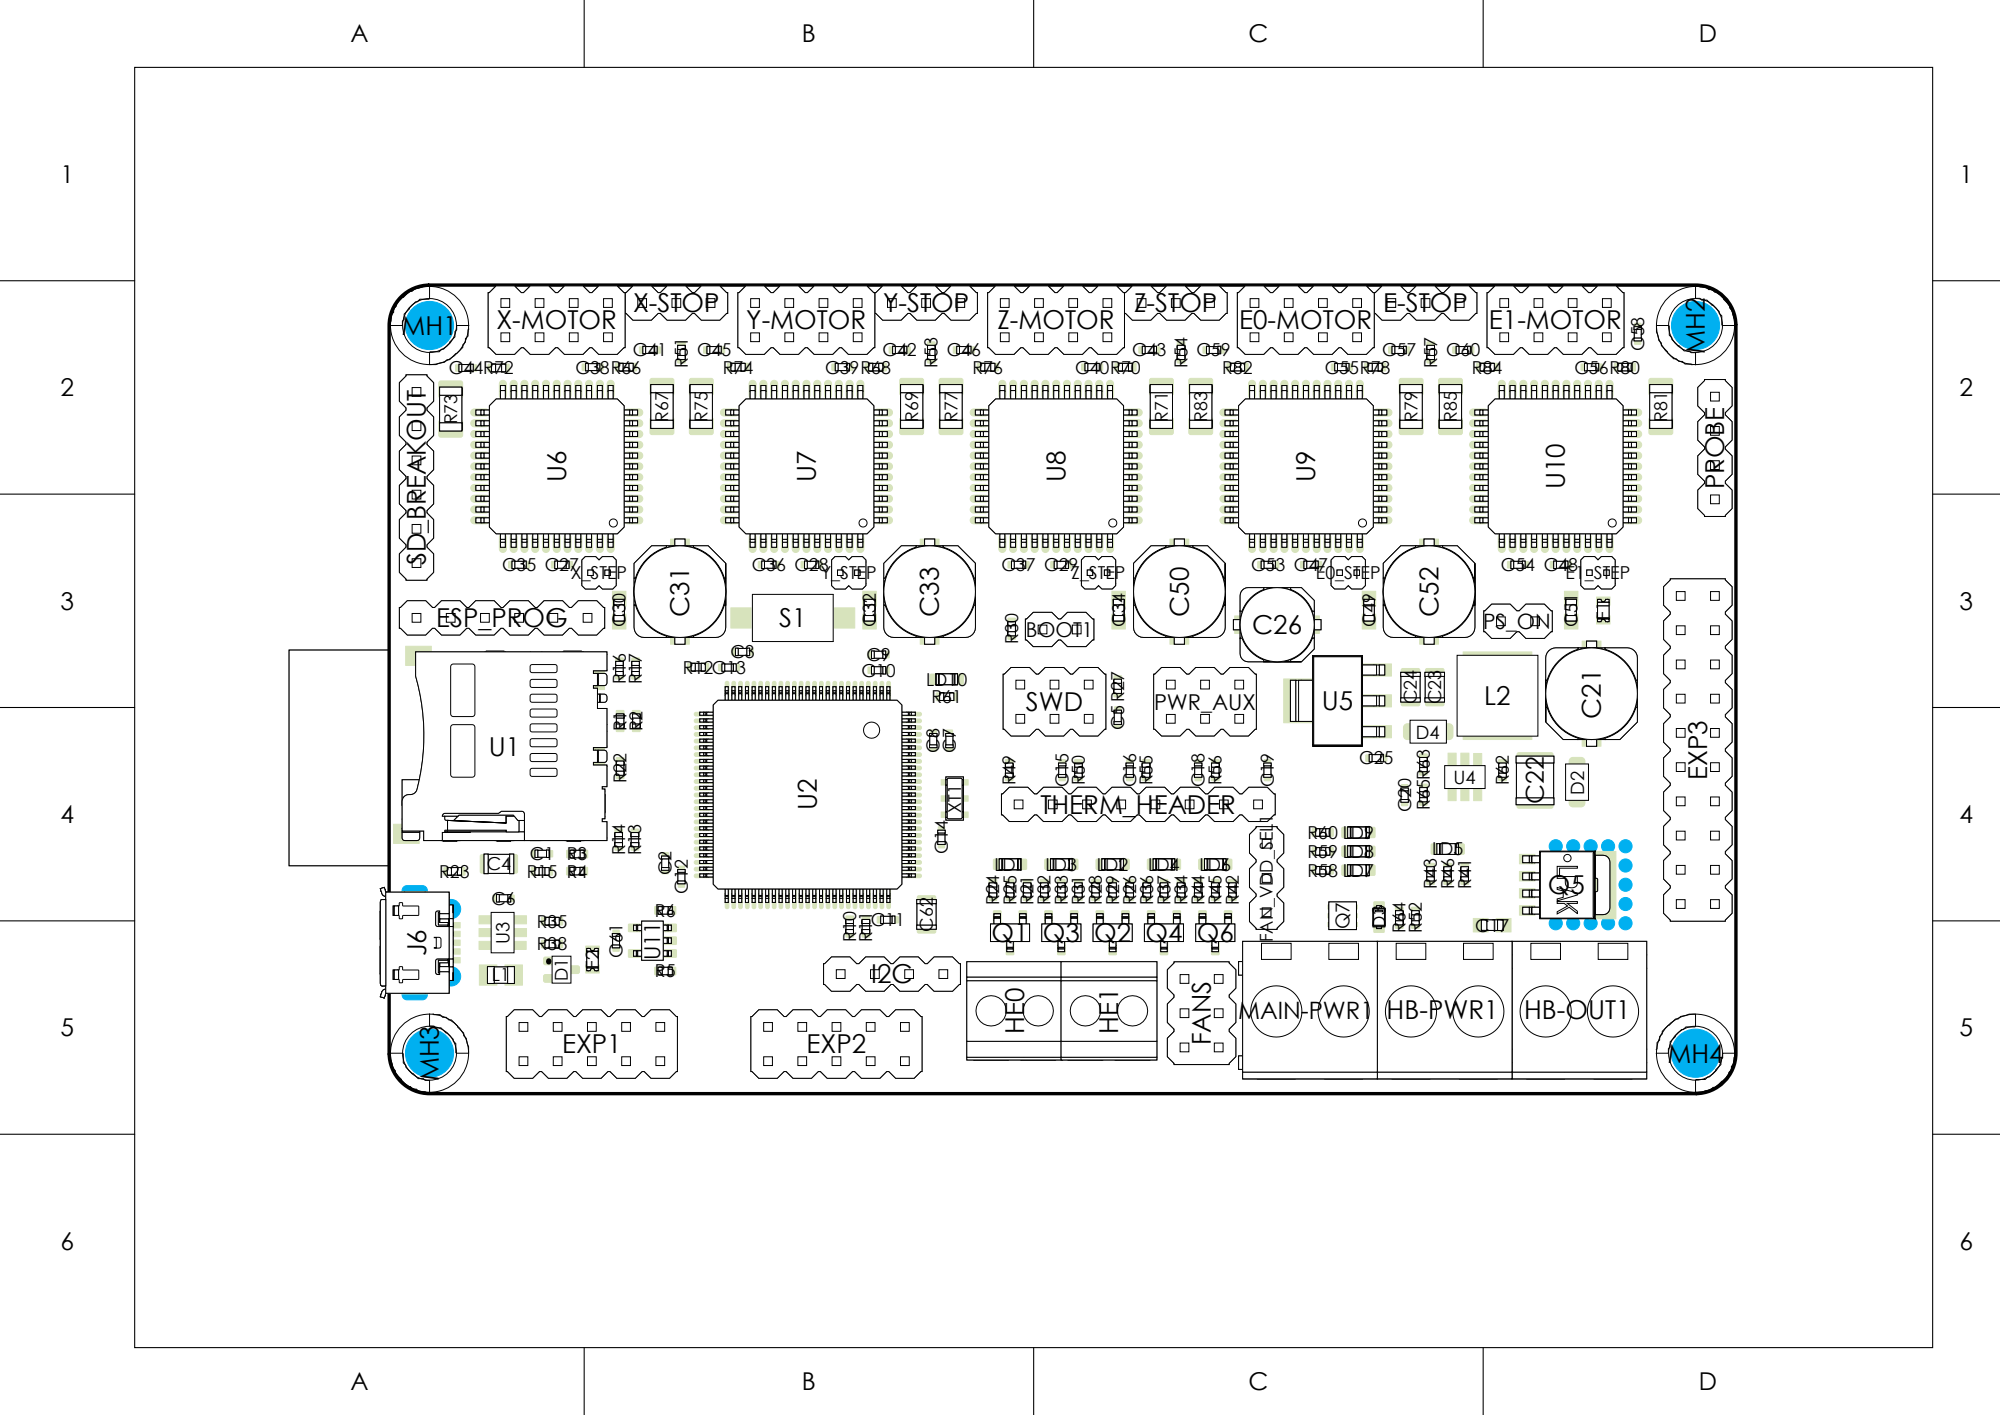
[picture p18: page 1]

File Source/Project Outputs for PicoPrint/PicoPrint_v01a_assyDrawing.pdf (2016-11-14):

A

B

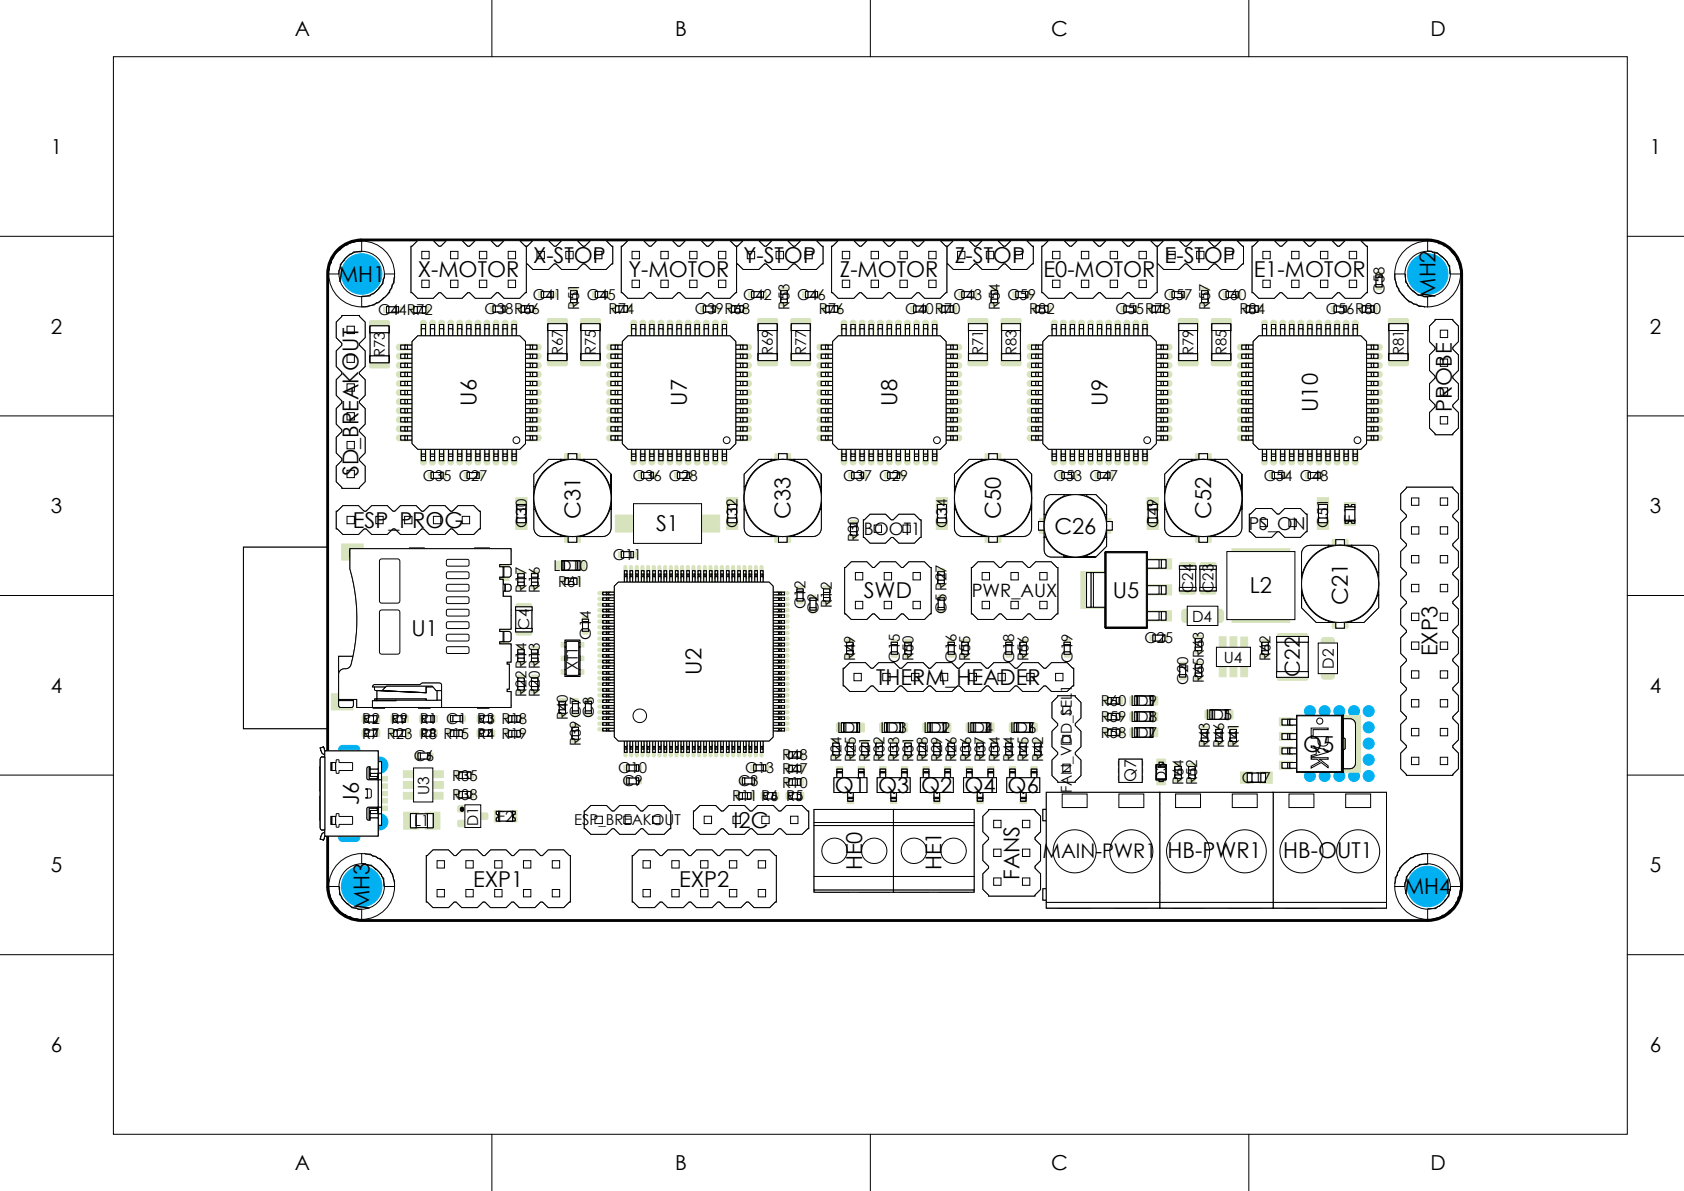
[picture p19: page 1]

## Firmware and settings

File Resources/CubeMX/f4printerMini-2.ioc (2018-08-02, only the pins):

Mcu.UserName=STM32F446VETx
PA0-WKUP.GPIO_Label=F1_PWM
PA0-WKUP.Signal=S_TIM5_CH1
PA1.GPIO_Label=F2_PWM
PA1.Signal=S_TIM5_CH2
PA10.Signal=USART1_RX
PA11.Signal=USB_OTG_FS_DM
PA12.Signal=USB_OTG_FS_DP
PA13.Signal=SYS_JTMS-SWDIO
PA14.Signal=SYS_JTCK-SWCLK
PA15.GPIO_Label=SERVO
PA15.Signal=GPIO_Output
PA2.GPIO_Label=PWR_MON
PA2.Signal=ADCx_IN2
PA3.GPIO_Label=Z_PROBE_A
PA3.Signal=ADCx_IN3
PA4.GPIO_Label=Z_PROBE_D
PA4.Signal=GPXTI4
PA5.Signal=SPI1_SCK
PA6.Signal=SPI1_MISO
PA7.Signal=SPI1_MOSI
PA8.GPIO_Label=USD_CD
PA8.Signal=GPIO_Input
PA9.Signal=USART1_TX
PB0.GPIO_Label=E1_CS
PB0.Signal=GPIO_Output
PB1.GPIO_Label=E0_STEP
PB1.Signal=GPIO_Output
PB10.GPIO_Label=Z_DIR
PB10.Signal=GPIO_Output
PB14.GPIO_Label=STAT_LED
PB14.Signal=GPIO_Output
PB15.GPIO_Label=USD_CS
PB15.Signal=GPIO_Output
PB2.GPIO_Label=E0_DIR
PB2.Signal=GPIO_Output
PB3.Signal=SPI3_SCK
PB4.Signal=SPI3_MISO
PB5.Signal=SPI3_MOSI
PB6.GPIO_Label=SD_CSEL
PB6.Signal=GPIO_Output
PB7.GPIO_Label=SD_DET
PB7.Signal=GPIO_Input
PB8.Signal=I2C1_SCL
PB9.Signal=I2C1_SDA
PC0.GPIO_Label=THERM3
PC0.Signal=ADCx_IN10
PC1.GPIO_Label=THERM2
PC1.Signal=ADCx_IN11
PC11.GPIO_Label=BTN_ENC
PC11.Signal=GPXTI11
PC12.GPIO_Label=LCD_RS
PC12.Signal=GPIO_Output
PC13.GPIO_Label=E2_STEP
PC13.Signal=GPIO_Output
PC14-OSC32_IN.GPIO_Label=E2_DIR
PC14-OSC32_IN.Signal=GPIO_Output
PC15-OSC32_OUT.GPIO_Label=E2_CS
PC15-OSC32_OUT.Signal=GPIO_Output
PC2.GPIO_Label=THERM1
PC2.Signal=ADCx_IN12
PC3.GPIO_Label=THERM0
PC3.Signal=ADCx_IN13
PC4.GPIO_Label=E1_STEP
PC4.Signal=GPIO_Output
PC5.GPIO_Label=E1_DIR
PC5.Signal=GPIO_Output
PC6.GPIO_Label=X_STEP
PC6.Signal=GPIO_Output
PC7.GPIO_Label=X_DIR
PC7.Signal=GPIO_Output
PC8.GPIO_Label=X_CS
PC8.Signal=GPIO_Output
PC9.GPIO_Label=BUZZER
PC9.Signal=S_TIM8_CH4
PD0.GPIO_Label=BTN_EN2
PD0.Signal=GPXTI0
PD1.GPIO_Label=LCD_D4
PD1.Signal=GPXTI1
PD10.GPIO_Label=Y_DIR
PD10.Signal=GPIO_Output
PD11.GPIO_Label=Y_CS
PD11.Signal=GPIO_Output
PD12.GPIO_Label=HB_PWM
PD12.Signal=S_TIM4_CH1
PD13.GPIO_Label=F0_PWM
PD13.Signal=S_TIM4_CH2
PD14.GPIO_Label=H1_PWM
PD14.Signal=S_TIM4_CH3
PD15.GPIO_Label=H0_PWM
PD15.Signal=S_TIM4_CH4
PD2.GPIO_Label=LCD_D5
PD2.Signal=GPXTI2
PD3.GPIO_Label=LCD_D6
PD3.Signal=GPXTI3
PD4.GPIO_Label=LCD_D7
PD4.Signal=GPIO_Output
PD5.GPIO_Label=KILL
PD5.Signal=GPXTI5
PD6.GPIO_Label=BTN_EN1
PD6.Signal=GPXTI6
PD7.GPIO_Label=LCD_EN
PD7.Signal=GPIO_Output
PD8.GPIO_Label=Z_CS
PD8.Signal=GPIO_Output
PD9.GPIO_Label=Y_STEP
PD9.Signal=GPIO_Output
PE0.GPIO_Label=PS_ON
PE0.Signal=GPIO_Output
PE1.GPIO_Label=E4_STEP
PE1.Signal=GPIO_Output
PE10.GPIO_Label=X_STOP
PE10.Signal=GPXTI10
PE11.GPIO_Label=E0_CS
PE11.Signal=GPIO_Output
PE12.Signal=SPI4_SCK
PE13.Signal=SPI4_MISO
PE14.Signal=SPI4_MOSI
PE15.GPIO_Label=Z_STEP
PE15.Signal=GPIO_Output
PE2.GPIO_Label=E4_DIR
PE2.Signal=GPIO_Output
PE3.GPIO_Label=E4_CS
PE3.Signal=GPIO_Output
PE4.GPIO_Label=E3_DIR
PE4.Signal=GPIO_Output
PE5.GPIO_Label=E3_STEP
PE5.Signal=GPIO_Output
PE6.GPIO_Label=E3_CS
PE6.Signal=GPIO_Output
PE7.GPIO_Label=E_STOP
PE7.Signal=GPXTI7
PE8.GPIO_Label=Z_STOP
PE8.Signal=GPXTI8
PE9.GPIO_Label=Y_STOP
PE9.Signal=GPXTI9
PH0-OSC_IN.Signal=RCC_OSC_IN
PH1-OSC_OUT.Signal=RCC_OSC_OUT

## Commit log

2016-10-19 Initial progress
    [R32-Micro.PrjPCB, R32-Micro.SchDoc, stepperDrivers.SchDoc]
2016-10-20 WIP
    Add E-Stop, use pin on EXP3
    Adjust jumpers
    Board layout improvements
    Tidy schematics
    [R32-Micro.PrjPCB, R32-Micro.SchDoc, stepperDrivers.SchDoc]
2016-10-20 Add solder jumper for fan voltage selection / current capacity
    [R32-Micro.SchDoc]
2016-10-21 Tidy schematic and PCB
    [R32-Micro.SchDoc, stepperDrivers.SchDoc]
2016-10-21 Tidy Schematics
    Change size of main sheet to A2. Would prefer several separate smaller sheets, but this will do for now.
    [R32-Micro.SchDoc, stepperDrivers.SchDoc]
2016-10-21 Improve heat dissipation on stepper drivers
    Adjust size of polygons to more evenly distribute heat.
2016-10-21 Improve routing
    Straighten and tidy some traces
    Adjust vias to increase thickness of Vin pour to stepper drivers
    Move some signals off of power layers
2016-10-21 Improve routing + fix endstops
    Fix error with endstops power connection
    Move more signals off of power layers
    Tidy routing
    [R32-Micro.SchDoc]
2016-10-22 Improvements
    Improve 5V and 3.3V regulators connections to ground + Vin / improve heat dissipation.
    Tidy routing.
    Tidy schematic.
    [R32-Micro.SchDoc]
2016-10-22 Add power to SDIO header
    [R32-Micro.SchDoc]
2016-10-23 Improve stepper driver heatsinking + tidying
    Increase size of stepper driver pours / polygons on top and bottom layers.
    Add additional silk-screen labels.
    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
2016-10-23 Improve MOSFET heatsinking
    Rework copper polygons / pours under HE0 - F2 MOSFETs. Increased copper area for each MOSFET, added additional copper on bottom of PCB and linked with thermal vias.
2016-10-24 Add component library
    Add library for all parts in design
    Update all resistors to correct 0402 parts (with BOM)
    [R32-Micro.PrjPCB, R32-Micro.SchDoc, stepperDrivers.SchDoc]
2016-10-26 BOM update
    Update all components to refer to included library files.
    Update all components to correct part numbers (some 0402 parts referred to 0603 components, etc)
    [R32-Micro.PrjPCB, R32-Micro.SchDoc, stepperDrivers.SchDoc]
2016-10-27 Fuse endstops + USB
    Add PTC fuses to endstop and USB power rails.
    Endstops are commonly shorted on RAMPS potentially causing damage - let's avoid this.
    Also need to protect USB host from overcurrent (though host should have fuses anyway, but this seems more polite...)
    [R32-Micro.SchDoc]
2016-10-28 Reverse polarity protection
    P-channel MOSFET on main power input to disconnect power when polarity is incorrect.
    Heated bed ground is now isolated from main ground of board, so that reversing bed power but not main power won't short Vin to ground. May need to consider what happens if someone is using separate power supplies for main power and bed power (do grounds need to be tied together)
    Updated / added to board silkscreen
    [R32-Micro.SchDoc]
2016-10-28 Add fuse part number
    [R32-Micro.SchDoc]
2016-10-28 Option to tie GND to Bed_GND
    [R32-Micro.SchDoc]
2016-11-13 Rework
    Remove one of the electrolytic capacitors for the motor power supply, creating more space for expansion header. Other capacitors moved around a lot, and many other components / routing effected too.
    Now there are 4 electrolytic caps between 5 stepper drivers, but total capacitance is still higher than suggested by datasheet / demo board.
    Removed jumper pads that allowed for disconnecting USB power from 5V rail. No real reason that should need to be done, and if it is diode can be removed anyway.
    [R32-Micro.SchDoc, stepperDrivers.SchDoc]
2016-11-14 Prototype board
    [Pick Place for R32-Micro.csv, R32-Micro-BOM.xlsx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]
2017-02-09 Tidying
    Update file/folder names
    Updated title block on schematic
    [Pick Place for R32-Micro-V02.csv, Pick Place for R32-Micro.csv, PicoPrint-Main.SchDoc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]
2017-10-15 Overhaul voltage regulators
    - Change 3.3V LDO from AP2114H to AP2112K
    -- Smaller package
    - Combine C23 and C24 into one larger capacitor
    - Tidy schematic layout of regulator section
    [PicoPrint-Main.SchDoc]
2017-10-15 Change D2, D4
    Change diodes D2 and D4 from DB2W40200L to SS24FL. Comparable or better specifications, slightly cheaper.
    [PicoPrint-Main.SchDoc]
2017-12-04 Schematic work
    Most changes for next revision done on schematic level.
    [PicoPrint-Connectors.SchDoc, PicoPrint-MOSFETs.SchDoc, PicoPrint-Main.SchDoc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]
2017-12-27 Layout work + schematic update
    Implemented schematic design in PCB layout, some back-and-forth resulting in changes to schematic as well.
    This is a draft placement of components on the board, with some routing to test things. Most routing remains to be done.
    [PicoPrint-Connectors.SchDoc, PicoPrint-MOSFETs.SchDoc, PicoPrint-Main.SchDoc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]
2018-04-06 Ongoing work
    [PicoPrint-Connectors.SchDoc, PicoPrint-MOSFETs.SchDoc, PicoPrint-Main.SchDoc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]
2018-04-06 Share SD SPI between internal and external cards
    [PicoPrint-Connectors.SchDoc, PicoPrint-Main.SchDoc]
2018-04-24 Change X driver to TMC2130-LA, initial routing draft
    [PicoPrint-Main.SchDoc, PicoPrint-Motors.SchDoc]
2018-04-30 Ongoing TMC2130 work
    [PicoPrint-Main.SchDoc, PicoPrint-Motors.SchDoc]
2018-04-30 Update all drivers to TMC2130-LA
    [PicoPrint-Motors.SchDoc]
2018-04-30 Motor driver component designators updated
    Still need to link and update all copper
    [PicoPrint-Main.SchDoc]
2018-04-30 Position and route TMC2130-LA drivers
2018-04-30 TMC2130-LA routing done
    Possibly some tidying up to do, but should all be functional now.
    [PicoPrint-Connectors.SchDoc, PicoPrint-Main.SchDoc, PicoPrint.PrjPCB]
2018-04-30 Tidying
    Tidy routing and labels
    [PicoPrint.PrjPCB]
2018-05-01 Tidy project outputs
    [PicoPrint_v01a_BOM.xlsx, PicoPrint_v02a_BOM.xlsx, PicoPrint_v02a_PickPlace.csv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]
2018-05-01 V0.3a BOM
    [PicoPrint-Connectors.SchDoc, PicoPrint-MOSFETs.SchDoc, PicoPrint-Main.SchDoc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]
2018-05-01 Update PDF schematic
    [PicoPrint-Main.SchDoc]
2018-05-01 Add and tidy Gerbers
    [PicoPrint.PrjPCB]
2018-05-01 Add assembly drawing
2018-05-01 Add Pick&Place file
    [PicoPrint_v03a_PickPlace.csv]
2018-05-03 Tidy schematics + PDFs
    Increase font sizes on schematics and centralise notes where possible, aiming to make schematics easier to read when printed at A4 scale.
    [PicoPrint-Connectors.SchDoc, PicoPrint-MOSFETs.SchDoc, PicoPrint-Main.SchDoc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]
2018-05-28 Tidy schematics
    Add MOSFET calculations
    Change some port directions
    [PicoPrint-MOSFETs.SchDoc, PicoPrint-Main.SchDoc]
2018-07-23 Prototype Files
    Files used for v0.3 prototype
    [PicoPrint-Connectors.SchDoc, PicoPrint-MOSFETs.SchDoc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]
2018-07-23 Prototype Fixes
    Initial fixes from manufacturing prototype:
    Add D14 to BOM
    Change LEDs in BOM to 0402 parts (pads are for 0402, previous BOM items were 0603)
    Tidy diode naming in BOM + some other parts
    Regenerate BOM from source files
    [PicoPrint-MOSFETs.SchDoc, PicoPrint-Main.SchDoc, PicoPrint-Power.SchDoc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]
2018-08-02 Tidying files
    Remove unneeded BOM documents
    Move CubeMX file to new resources folder
    Remove preview files
    [PicoPrint.PrjPCB]
2018-08-03 Update README.md
    Add current specifications
    Needs tidying
2018-08-23 Update to v0.3c
    Fix part number for bed MOSFET
    Change series resistors in voltage-clipping circuits from 1K to 4K7 to reduce power dissipation
    Remove fuse and capacitor on endstop power rail (largely redundant as 5V and 3V regulators have short protection)
    Change 3.5mm screw terminals to Pheonix Contact 1984617
    Change capacitors around stepper power rail ferrite
    [PicoPrint-Connectors.SchDoc, PicoPrint-MOSFETs.SchDoc, PicoPrint-Main.SchDoc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]
